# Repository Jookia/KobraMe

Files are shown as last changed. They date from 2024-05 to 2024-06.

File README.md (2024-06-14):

KobraMe
-------

This is my adapter for mounting the Hero Me Gen7 to the Anycubic Kobra. The files are in [FreeCAD](https://www.freecad.org/) format, assembled with the [Assembly4](https://wiki.freecad.org/Assembly4_Workbench) workbench and using parts from the [Fasteners Workbench](https://wiki.freecad.org/Fasteners_Workbench).

Here's the adapter just screwed in to the Kobra's carriage:

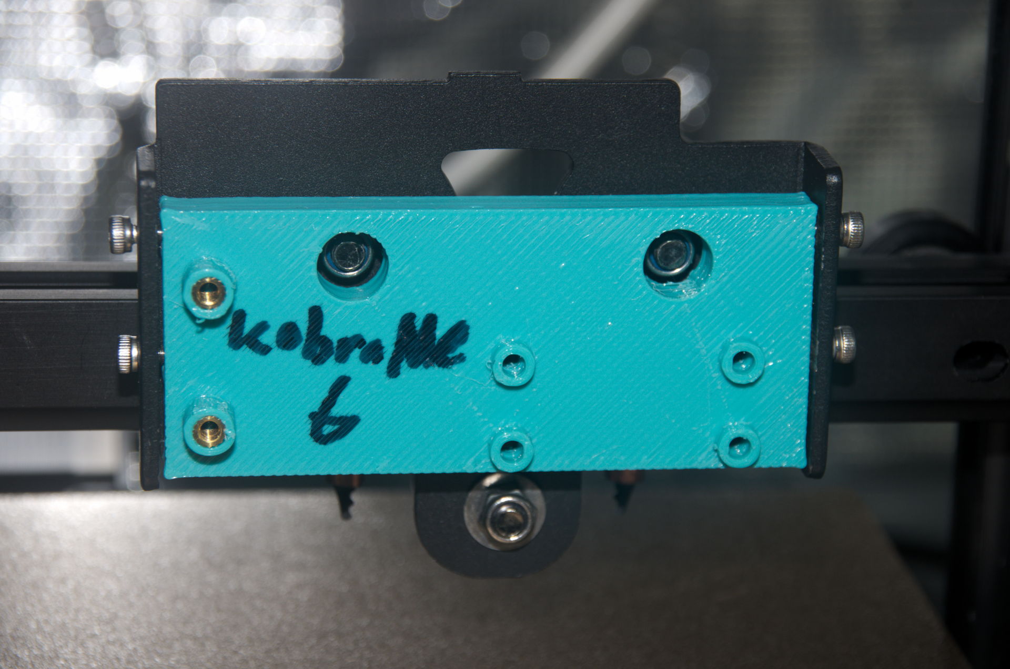
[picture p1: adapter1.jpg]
A plastic rectangular teal block sits in a 3D printer toolhead carriage. It has the text 'KobraMe 6' scrawled on it in marker. The block has two large holes for the carriage's back hole, two heat set screw holes for the toolhead PCB on the left, and four raised holes for the Hero Me base on the rig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


Here's the toolhead PCB and Hero Me screwed on to the adapter.

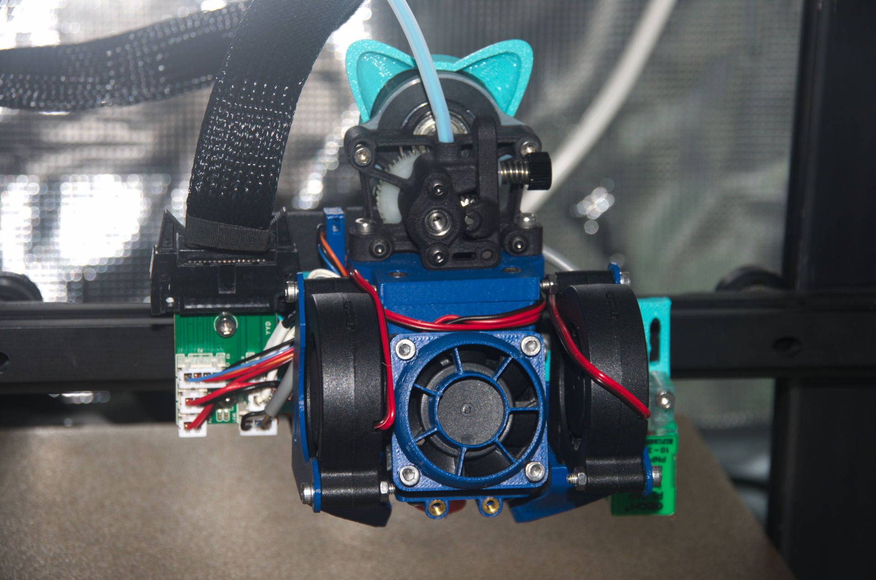
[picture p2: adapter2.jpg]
A standard Hero Me adapter made out of a mix of dark blue and teal plastic hangs in the air. The wires from its components connect to a toolhead PCB to its left. Both are mounted against a hidden toolhead adapter. A set of teal cat ears sit on top of the extruder.


Usage guide
-----------

You will need:

- 1x A Hero Me Gen7
- 6x M3 heat sets
- 6x M3 8mm screws (optional, the Kobra toolhead screws will work)

Printing guide:

1. Load one of the PRINT_ME files in to your slicer
1. Slice as usual, no supports are needed
1. Print the adapter
1. Insert heat sets in to the sides and PCB holes
1. Remove sacrifical plastic from the base holes

Assembly guide:

1. Unplug, remove and disassemble the Kobra's toolhead
1. Disconnect and remove the toolhead PCB from the Kobra's toolhead
1. Screw the toolhead PCB into the adapter
1. Screw the Hero Me base into the adapter
1. Hold and line up the assembled adapter up with the carriage's holes
1. Partially screw in the top right screw
1. Partially screw in the bottom left screw
1. Partially screw in the other two screws
1. Fully screw in all screws
1. Connect the PCB adapter

Modification guide:

1. Install FreeCAD
2. Open ```Adapter.FCstd```
3. Make your desired modifications 
4. Click on the EXPORT_ME object
5. Open the File menu and click Export

Extras
------

Running the Hero Me on your printer will require custom firmware. The easiest way to do this is using Klipper. Unfortunately mainline Klipper does not work on the Kobra.

I work on and recommend [Catboat](https://github.com/printers-for-people/catboat), a fork of Klipper that works on the printer without any hardware modification.

I also recommend putting Koz's [Moons motor cat ears](https://www.printables.com/model/430159-moons-motor-cat-ears) on your printer. Nyan!

Hero Me License
---------------

The HeroMe.FCStd contains contains content from the [Hero Me Gen7](https://www.printables.com/model/39322-hero-me-gen-7-platform-release-4) project.

Hero Me Gen7 is copyright 2023 Andrew Soderberg, released under the [CC BY-NC-SA 4.0 International](https://creativecommons.org/licenses/by-nc-sa/4.0/) license. A copy of this license can be found in the ```CC-BY-NC-SA-4.0.txt``` file.

This project modifies this content to create a FreeCAD assembly for measurements. These modifications are also licensed under the CC BY-NC-SA and are copyright 2023 Jookia.

KobraMe License
---------------

Excluding HeroMe.FCStd, KobraMe is copyright 2024 [Jookia](mailto:contact@jookia.org) and released under the [CC BY-SA 4.0 International](https://creativecommons.org/licenses/by-sa/4.0/) license. A copy of this license can be found in the ```CC-BY-SA-4.0.txt``` file.

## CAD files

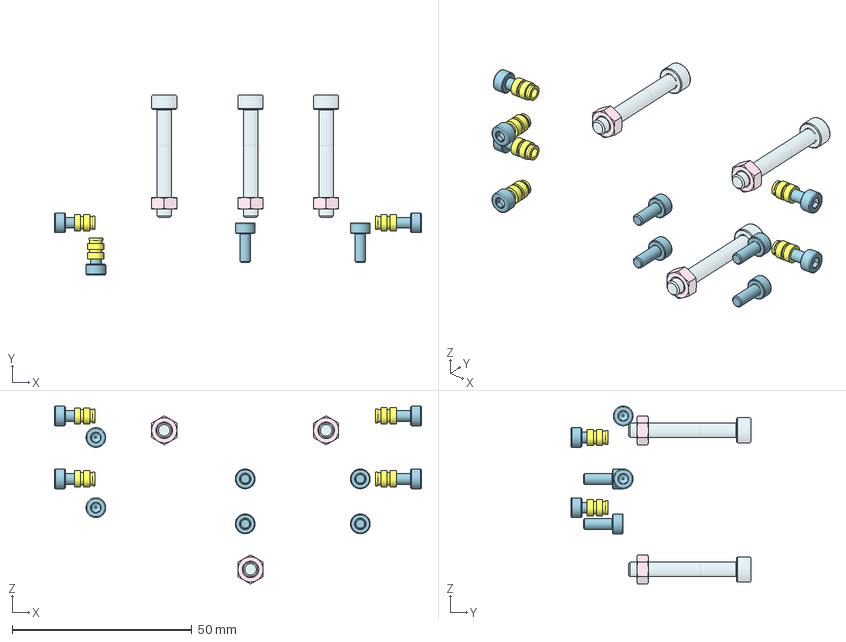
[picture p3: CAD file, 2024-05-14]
Assembly.FCStd
102.0 x 50.0 x 49.5 mm
M3x6-Screw x 12
M4x30-Screw x 9
M4-Nut x 9
M3x8-Screw x 12
M3x6-Screw037 x 6
M3-Insert x 18

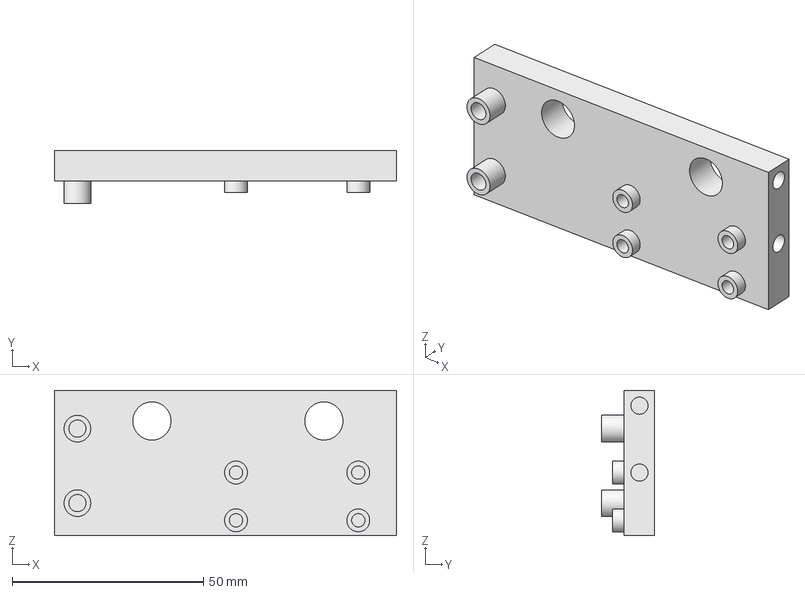
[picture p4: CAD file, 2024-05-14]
PRINT_ME.step
89.5 x 14.0 x 38.0 mm

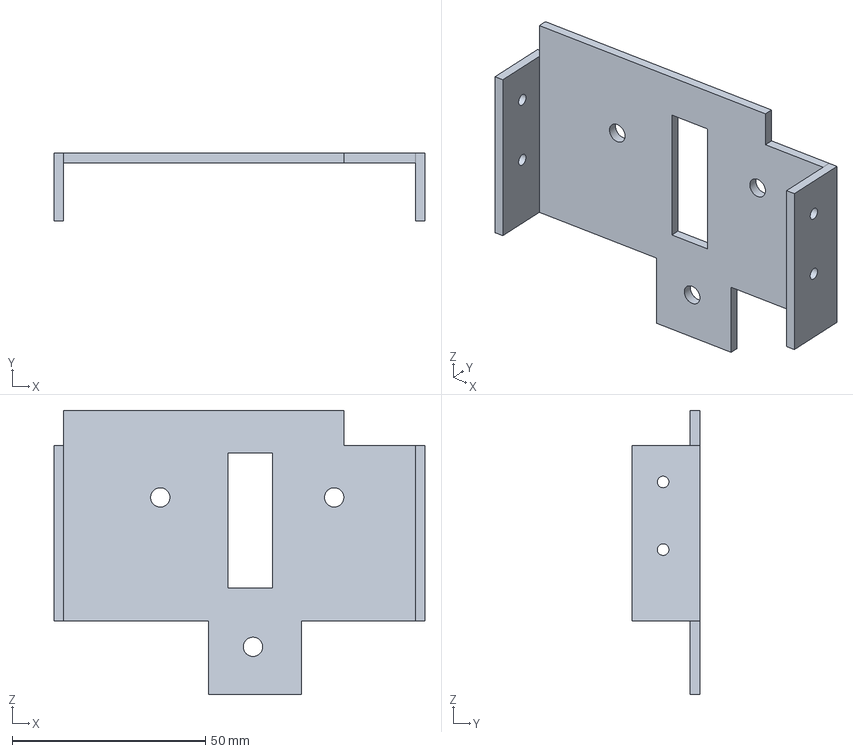
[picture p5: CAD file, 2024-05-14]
Carriage.FCStd
96.0 x 17.5 x 73.5 mm

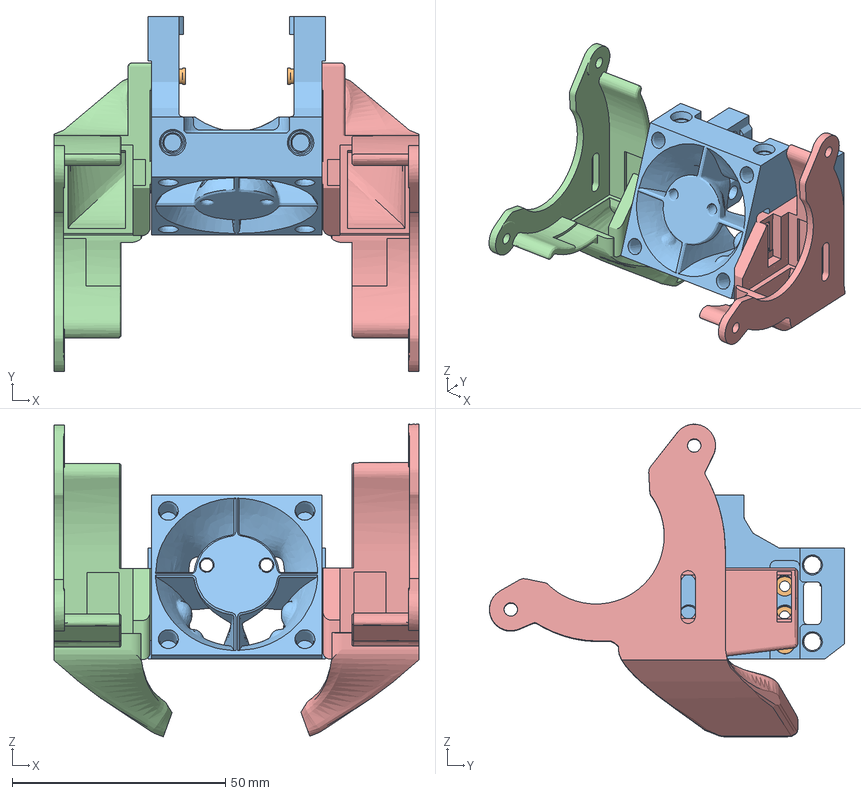
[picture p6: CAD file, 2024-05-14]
HeroMe.FCStd
85.5 x 83.2 x 73.3 mm
M3-Insert x 8
M3-Insert017 x 12
HMG7.2 Universal Base V2
HMG7.3 Standard Single 5015 Left Duct V3
HMG7.3 Standard Single 5015 Right Duct V3

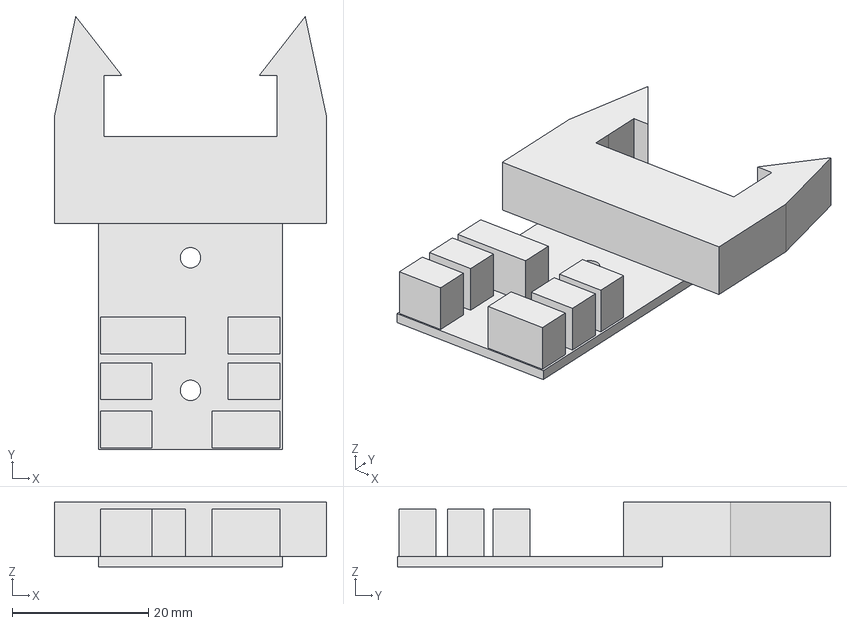
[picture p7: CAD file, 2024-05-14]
ToolheadPCB.FCStd
40.0 x 63.7 x 9.50 mm

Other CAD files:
Adapter.FCStd
PRINT_ME.3mf
PRINT_ME.stl

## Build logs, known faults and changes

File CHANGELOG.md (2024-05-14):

Release1 (14-05-2024)
-------------------

Just a fixup for a public release.

Changes:

- Changed EXPORT_ME to rotate properly
- Added exports of files
- Added documentation and photos

Problems:

- None?

Print6 (12-05-2024)
-------------------

Another attempt at back holes. It fits!

Changes:

- Moved back holes

Problems:

- None?

Print5 (08-05-2024)
-------------------

Another attempt at the back holes.

Changes:

- Made adapter thicker
- Made base holes shorter
- Replaced back indents with holes
- Remade sacrifical layers

Problems:

- Back holes are too far right

Print4 (31-10-2023)
-------------------

Another attempt at the back holes.

Changes:

- Made back indents larger
- Made toolhead PCB holes higher
- Added sacrifical layers

Problems:

- Indents are too far left
- Indents are too shallow

Print3 (09-07-2023)
-------------------

After cutting the indents I managed to mount this to the printer and confirm it works.

Changes:

- Added supports for base holes
- Added indents for back holes
- Widened toolhead PCB holes

Problems:

- Indents are too far left
- Indents are too small

Print2 (05-07-2023)
-------------------

Second attempt.

Changes:

- Made adapter narrower
- Made adapter much shorter
- Made toolhead PCB holes much thinner

Problems:

- Hero Me probe bumps side of carriage
- Side heat sets make the plastic bulge
- Carriage screws block the adapter

Print1 (04-07-2023)
-------------------

Initial revision.

Problems:

- The width of the adapter is too wide
- The side screws are too close together
